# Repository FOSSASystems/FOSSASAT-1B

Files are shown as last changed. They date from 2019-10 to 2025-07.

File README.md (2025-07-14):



[Doxygen Documentation](https://fossasystems.github.io/FOSSASAT-1B)

## FOSSASAT-1B

FOSSASAT-1B is slightly modified second iteration of the FOSSASAT-1 satellite launched in December of 2019. It is set to launch with FOSSASAT-2 aboard the Alpha Firefly rocket in Q2-3 2020 into a 300km LEO orbit. The following differences are listed:

- Use of IXYS Cells instead of TrisolX
- No deployable Solar Panels
- Use of a new through-hole burnwire resistor
- Diodes added in MPPT
- DRF1268 has RST and SW connections modified
- Added Watchdog external connection for programming
- Passive attitude control re-designed

<br>
Picture of FOSSASAT-1B (Left) next to FOSSASAT-2
<br>
<br>


<br>

## Launch

FOSSASAT-1B was initially launched in the maiden mission of the firefly Alpha which experienced in an in-flight failure, subsequently it was launched into space on a second Firefly Alpha vehicle in October of 2022. Below is the first packet received from space! The satellite re-entered after 2 days in orbit due to a low insertion altitude. 

<br>

<br>

## Hardware

PCBs and Schematics are designed using EasyEDA, Java files are available for using them in said interface. 

## Software

The design of the FOSSASAT-1 code is a minimalist C-type structure. Everything is contained within code files whos name represents the functionality of the funtions within.

The core of the communications system uses a large switch that routes received messages to function calls.

The system has a large amount of configuration defines that control all aspects, this is found in the configuration.h/.cpp which again is documented thoroughly to describe it. There is a single function within the configuration "module" that controls the pin setups that can be found here: https://github.com/FOSSASystems/FOSSASAT-1B/blob/master/software/FossaSat1B/configuration.cpp#L32

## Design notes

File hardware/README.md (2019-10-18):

# FOSSASAT-1B Hardware
This folder contains all schematic, layout and mechanical files related to FOSSASAT-1B.

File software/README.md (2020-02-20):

# FOSSASAT-1B Software
This folder contains all software related to FOSSASAT-1B, on-board or otherwise.

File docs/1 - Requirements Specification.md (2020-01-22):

# 1 - Requirements

## Changelog

|Date|Description|Author|
|--|--|--|
|08/01/2020|Created initial document.|RB|
|08/01/2020|Added HREQ1 to HREQ25.|RB|
|08/01/2020|Added LREQ1 to LREQ5.|RB|
|08/01/2020|Merged FOSSASAT-1 requirements.|RB|
|09/01/2020|Modified requirement for transmissions modes to CW and FSK|RB|

## High Level Requirements Specification
|ID|Description|Author|Functional Requirements (Y/N)|Reference IDs|
|--|--|--|--|--|
|HREQ1|The satellite shall communicate with other generic and widely used radio systems.|RB|Y||
|HREQ2|The satellite must be able to be silenced with a radio command.|RB|Y||
|HREQ3|The satellite must transmit with a callsign.|RB|Y||
|HREQ4|The satellite must protect sensitive commands with encryption|RB|Y||
|HREQ5|The satellite must be able to operate from a battery.|RB|Y||
|HREQ6|The satellite must be able to re-charge the battery using solar panels.|RB|Y||
|HREQ7|The satellite must deploy its antenna|RB|Y||
|HREQ8|The satellite must be able to give a ground station its system information on command.|RB|Y||
|HREQ9|The radio power and operation shall not exceed or violate the regulated standards.|RB|Y||
|HREQ10|The radio communications shall not harm other radio communicating devices.|RB|Y||
|HREQ11|The satellite must be able to restart on command.|RB|Y||
|HREQ12|The satellite must be able to operate with no MCU issues such as memory leaking or halting.|RB|Y||
|HREQ13|The satellite must power on once it is jettisonned|RB|Y||
|HREQ14|The satellite must be able to orbit for at least 1 year.|RB|Y||
|HREQ15|The satellite's radio must be able to be configured remotely.|RB|Y||
|HREQ16|The satellite must be able to handle software and hardware errors.|RB|Y||
|HREQ17|The communications protocol shall be open source.|RB|N||
|HREQ18|The communications protocol must be accessible and simple.|RB|N||
|HREQ19|There must be no malicious transmisions.|RB|N||
|HREQ20|The satellite must be able to operate in a low power mode.|RB|Y||
|HREQ21|The satellite's hardware must be able to withstand all operational conditions.|RB|Y||
|HREQ22|The satellites hardware must be destroy in the atmosphere when de-oribiting.|RB|Y||
|HREQ23|The satellite's oribtal TLE must be available to the public.|RB|Y||
|HREQ24|The satellite must be registered with Satnogs to ensure ground station coverage.|RB|N||
|HREQ25|The satellite must not affect other satellites during launch.|RB|Y||
|HREQ26|The satellite must be able to communicate using the FOSSA Protocol.|RB|Y||

## Low Level Requirements
|Requirement ID|Description|Functional (Y/N)|Author|Reference IDs|
|--|--|--|--|--|
|LREQ1|The satellite must be able to trasmit using CW|Y|RB||
|LREQ2|The satellite must be able to trasmit using GFSK|Y|RB||
|LREQ3|The battery must stop charging if the temperature goes below 0 degrees Celsius.|Y|RB||
|LREQ4|The satellite must enter a low power mode when not in use.|Y|RB||
|LREQ5|Low power mode must be saved and retrieved from EEPROM|Y|RB||
|LREQ6|The callsign must be saved and retrieved from EEPROM|Y|RB||
|LREQ7|The battery temperature switching state must be saced and retrieved from EEPROM.|Y|RB||
|LREQ8|The radio's frequency band must be able to switch between X.XXX, Y.YYY,Z.ZZZ.etc|Y|RB||
|LREQ9|The radio's spreading factor must be able to switch between X,Y,Z.etc|Y|RB||
|LREQ10|The radio's sync word must be compatible with all devices.|Y|RB||
|LREQ11|The satellite must be able to communicate using Morse Code.|Y|RB||
|LREQ12|The satellite must stop transmissions when X command received..|Y|RB||

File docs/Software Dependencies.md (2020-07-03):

# FOSSASAT-1B Software Dependencies
The following is a list of all libraries and other dependencies required to build software for FOSSASAT-1B.

## Platform & Core Libraries
* AVR core

## Libraries
* FOSSA-Comms: https://github.com/FOSSASystems/FOSSA-Comms
* RadioLib: https://github.com/jgromes/RadioLib
* tiny-AES-c: https://github.com/FOSSASystems/tiny-AES-c
* INA226: https://github.com/jarzebski/Arduino-INA226
* AVR Low Power: https://github.com/canique/Low-Power-Canique

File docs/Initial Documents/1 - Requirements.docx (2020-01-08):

# 1 – Requirements

FOSSASAT-1B

FOSSA Systems

# Changelog

Date | Description | Author
08/01/2020 | - Created initial document. - Added HREQ1 to HREQ25 - Added LREQ1 to LREQ5 - Merged initial requirements and separated into high and low level. | Richard Bamford

# High Level Requirements Specification

ID | Description | Author | Functional requirement? (Y/N) | Reference ID
HREQ1 | The satellite shall communicate with other generic and widely used radio systems. | Richard Bamford | Y
HREQ2 | The satellite must be able to be silenced via a command. | Richard Bamford | Y
HREQ3 | The satellite must transmit with a callsign for identification. | Richard Bamford | Y
HREQ4 | The satellite must protect sensitive commands with AES encryption. | Richard Bamford | Y
HREQ5 | The satellite must be able to operate from a battery. | Richard Bamford | Y
HREQ6 | The satellite must be able to re-charge using the solar panels. | Richard Bamford | Y
HREQ7 | The satellite must deploy its solar panels. | Richard Bamford | Y
HREQ8 | The satellite must be able to give a ground station its system information on command. | Richard Bamford | Y
HREQ9 | The radio power and operation shall not exceed or violate the regulated standards. | Richard Bamford | Y
HREQ10 | The radio communications shall not harm other radio communicating devices. | Richard Bamford | Y
HREQ11 | The satellite must be able to restart itself on command. | Richard Bamford | Y
HREQ12 | The satellite must be able to operate with no MCU issues such as memory leaking/halting. | Richard Bamford | Y
HREQ13 | The satellite must switch on once it is jettisoned. | Richard Bamford | Y
HREQ14 | The satellite must be able to orbit for at least 1 year. | Richard Bamford | Y
HREQ15 | The satellite’s radio must be able to be configured remotely. | Richard Bamford | Y
HREQ16 | The satellite must be able to handle software and hardware errors. | Richard Bamford | Y
HREQ17 | The communications protocol shall be open source. | Richard Bamford | N
HREQ18 | The communications protocol must be accessible and therefore simple. | Richard Bamford | N
HREQ19 | There shall be no malicious transmissions. | Richard Bamford | N
HREQ20 | The satellite must be able to operate at a low power mode. | Richard Bamford | Y
HREQ21 | The satellite’s hardware must be able to withstand operational conditions. | Richard Bamford | Y
HREQ22 | The satellite’s hardware must be destroyed on de-orbiting. | Richard Bamford | Y
HREQ23 | The satellite’s orbital TLE must be available to the public. | Richard Bamford | N
HREQ24 | The satellite must be registered with Satnogs to ensure ground station coverage. | Richard Bamford | Y
HREQ25 | The satellite must remain in a benign state during launch. | Richard Bamford | Y
HREQ26 | The satellite must be able to communicate using the FOSSA Protocol. | Richard Bamford | Y

# Low Level Requirements Specification

Requirement ID | Description | Author | Reference IDs
LREQ1 | The satellite must be able to transmit using RTTY. | Richard Bamford | HREQ1
LREQ2 | The satellite must be able to transmit using LoRa. | Richard Bamford | HREQ1
LREQ3 | The battery must stop charging if temperature goes below 0 degrees Celsius. | Richard Bamford | HREQ5
LREQ4 | The satellite must enter a low power mode when not in use. | Richard Bamford | HREQ14
LREQ5 | Low power mode must be saved and retrieved from EEPROM. | Richard Bamford
LREQ6 | Callsign must be saved and retrieved from EEPROM. | Richard Bamford
LREQ7 | The battery temperature switch must be saved and retrieved from EEPROM. | Richard Bamford
LREQ8 | The frequency band must be able to switch between X.XXX, Y.YYY, Z.ZZZ | Richard Bamford | HREQ1, HREQ9
LREQ9 | The spreading factor must be able to switch between X,Y,Z | Richard Bamford | HREQ9
LREQ10 | The sync word must be compatable with all devices, set to X | Richard Bamford
LREQ11 | The satellite must be able to communicate using Morse Code. | Richard Bamford | HREQ1
LREQ12 | The satellite must stop transmissions when X command received.

# Bibliography

There are no sources in the current document.

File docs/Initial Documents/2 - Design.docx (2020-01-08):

# 2 – Design

FOSSASAT-1B

FOSSA Systems

# Changelog

Date | Description | Author
08/01/2020 | - Created initial document. | Richard Bamford

# Protocol Design

# Software Design

# Hardware Design

# Bibliography

There are no sources in the current document.

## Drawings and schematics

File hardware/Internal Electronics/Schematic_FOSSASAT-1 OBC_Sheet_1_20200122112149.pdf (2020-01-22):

## DEPLOYMENT FET

UTILITY HEADER | PROGRAMMING HEADER

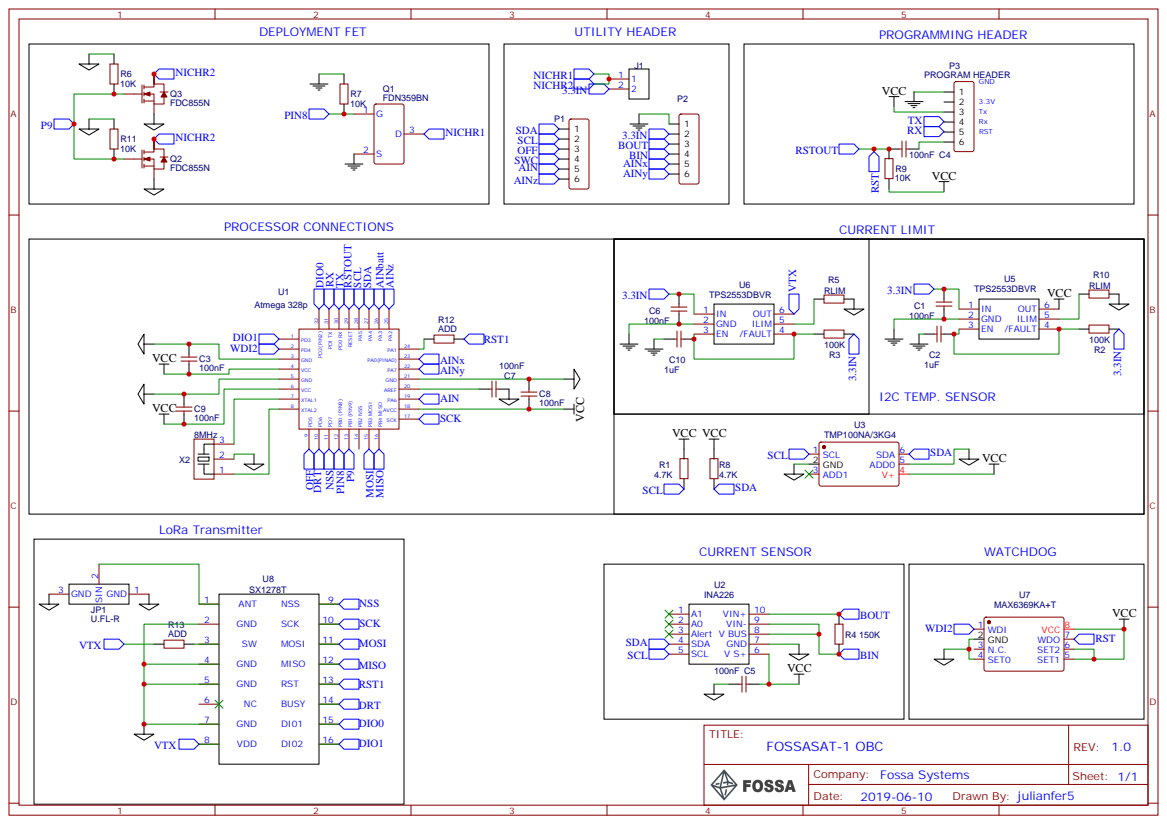
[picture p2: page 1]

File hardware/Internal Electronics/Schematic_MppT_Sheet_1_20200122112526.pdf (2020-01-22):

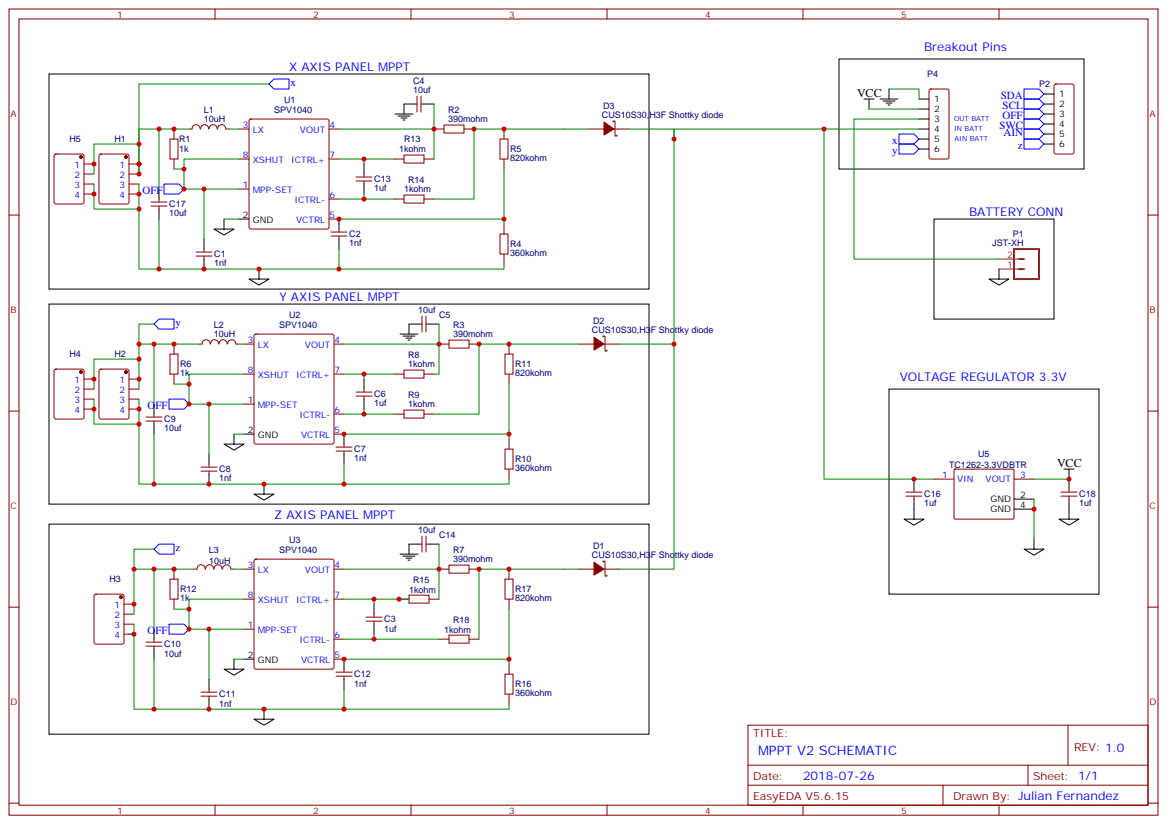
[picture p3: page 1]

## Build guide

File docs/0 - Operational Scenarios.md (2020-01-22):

# 0 - Operational Scenarios

## Changelog

|Date|Description|Author|
|--|--|--|
|08/01/2020|Created initial document.|RB|
|20/01/2020|Added initial Scenarios.|Julian Fernandez|

## On The Ground

See document 3. for testing to be carried out on the satellite before integration procedure.

|Name|Description|
|--|--|
|Integration Test|Satellite must be programmed, tested and charged beforehand, if neccesary due to time; check battery voltage via EGSE and serial output, antenna must not deploy in duration of test (3 minutes)|
|Integration Procedure|Satellite timer for deployer is reset via killswitches and then inserted into deployer. EEPROM counter still 0 as no deployment has occured|

## During Launch
|Name|Description|
|--|--|
|Storage Period|Satellite will stay in storage for several weeks without power with killswitches active|
|Launch|Satellite must withstand launch forces, no effect on Software|
## Jettison and Deployment
|Name|Description|
|--|--|
|Initial Jettison|Satellite is activated, Reset counter at 0 hence deployment procedure started|
|Deployment|If battery above x voltage When 3 minutes passed, burn wire for y seconds, else, wait for battery to reach y voltage.
|Wait time|During wait time, satellite is active but not transmitting (like in low power mode), it can recieve.
|Deployment Try 2|If time elapsed is more than 5 hours (timer integrated or cycle counter?), deploy in any case.
|Actual Deployment|When deployment command is carried out, start transmitting.

## Anomalies 
|Name|Description|
|--|--|
|In orbit resets|If satellite resets (can be issued by command or caused by watchdog), counter is increased. For the first 2 resets, deployment procedure occurs in the same manner as explained above|
|Deployment Command|Deployment Command bypasses voltage check|

## Orbital

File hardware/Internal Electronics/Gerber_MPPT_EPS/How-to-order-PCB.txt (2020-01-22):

How to Order PCB

Please refer to:
https://docs.easyeda.com/en/PCB/Order-PCB

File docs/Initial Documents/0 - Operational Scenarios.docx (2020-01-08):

# 0 – Operational Scenarios

FOSSASAT-1B

FOSSA Systems

# Changelog

Date | Description | Author
08/01/2020 | - Created initial document. | Richard Bamford

# On ground operation

# During launch operation

# Jettison operation

# Orbital operation

# Bibliography

There are no sources in the current document.

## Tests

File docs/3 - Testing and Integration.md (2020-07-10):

# 3 - Testing and Integration

## Changelog
|Date|Description|Author|
|--|--|--|
|08/01/2020|Created initial document.|RB|
|27/01/2020|Updated to include successful test result.|RB|
|5/07/2020|Entire test cases implemented in the software test system.|RB|
|06/07/2020|Added new document 3.1 Testing Additions|RB|

## Testing

Use your discretion when intrepreting the successful result of a test, if unsure, contact FOSSA Systems at our discord channel.

## Required Features for tests:

1. Controlling the temperature readings.
2. Controlling battery readings.
3. Checking whether deployment system has physically ran.
4. Detecting radio transmissions and interpreting them.
5. Manually making the satellite restart without losing test run.

### Main Program
|Reference ID|Description|Tested (Y/N)|Tested Date (dd-mm-yyyy|Status|Successful Result|Automated|
|--|--|--|--|--|--|--|
|MAINPROGT1|Startup configuration.||||Once the program has started, are all the pins, components and internal code configured correctly? Do they match the indended use?||
|MAINPROGT2|Test pin configuration.||||Do all pins attach to their intended component pin correctly?||
|MAINPROGT3|Test radio error mode handling.|||| Are all the radio exceptions created handled?| |
|MAINPROGT4|Confirm the MCU has enough resources to run the software.||||When the software is executed on the target hardware, does it run the entire program without having memory issues?.||
|MAINPROGT5|Check that the satellite transmits.|||| Can the satellite transmissions be received by a radio?
|MAINPROGT6|Check that the satellite can recieve trasmissions.|||| Can the satellite receive transmissions?|
|MAINPROGT7|Check that the radio re-configures successfully.||||When the radio is changed, does the satellite still transmit and receive correctly?|
|MAINPROGT8|Check that the MCU can be delayed by up to 10 minutes.||||When the satellite is delayed, does it react the way you intended?|
|MAINPROGT9|Check that the MCU can run the software system for at least a week.||||When you run the software on the related hardware, does it run how it should for a long time?| 
|MAINPROGT10|Check that the hardware watchdog is signalled correctly.||||Does the hardware watchdog cause any issues with restarting during its operation? For example causing restarts in long functions?|
|MAINPROGT11|Check that the hardware watchdog does not switch the satellite off during transmission.||||When the satellite transmits in any mode, does it correctly send transmissions without the watchdog interefering, even with long transmissions|
|MAINPROGT12|Check the software does not enter any restart loops.||||Does the code of the satellite enter any sections of code that cause it to restart over and over again? (check restart command useage)|

## Deployment
|Reference ID|Description|Tested (Y/N)|Tested Date (dd-mm-yyyy|Status|Successful Result|Automated|
|--|--|--|--|--|--|--|
|DEPLOYT1|Test the deployment sequence in scenarios; debugging, integration and jettison.||||Does the deployment sequence run correctly in these 3 scenarios? the debugging deployment sequence, integration and jettison sequences are different.|N - cannot simulate scenarios|
|DEPLOYT2|Check that the deployment sequence writes to the EEPROM.|||| When the deployment sequence runs in jettison mode, does it correctly save its state to the EEPROM?| Y |
|DEPLOYT3|Check that the deployment sequence does not run if the EEPROM state has been set.||||If the deployment sequence has ran, does it run again?|N - cannot test whether deployment has happened other than the EEPROM state.|
|DEPLOYT4|Check that the deployment sequence enable time is suitable.||||When the satellite powers the deployment mechanism, does it work correctly?|N - no way to measure whether the deployment sequence actually physically worked.|
|DEPLOYT5|Confirm that a system information transmission is sent before the deployment sequence begins.||||Before the deployment sequence begins, does it send a transmission to notify receivers that it is about to occur?|N - cannot test TX messages yet.|
|DEPLOYT6|Check that the deployment sequence transmits a success transmission afterwards.||||After the deployment sequence, does it tell receivers that it has occured?|N - cannot test radio TX.|
|DEPLOYT7|Check that the deployment system returns the correct value for its current state.||||When the satellite restarts, does it load the correct value from the EEPROM?|N - cannot simulate scenarios.|

## Power Control
|Reference ID|Description|Tested (Y/N)|Tested Date (dd-mm-yyyy|Status|Successfull Result|Automated|
|--|--|--|--|--|--|--|
|POWCONT1|Check the battery charging state changes when the temperature is >0 and <0 degrees Celsius.||||Simulate the sub-0 scenario by override the temperature sensor, does the battery charging react accordingly?|N - Cannot test this since we cannot simulate temperatures.|
|POWCONT12|Check the battery charging circuit (MPPT) is switched on and off correctly.||||When using the MPPT circuit, does it switch on and off without affecting other areas of code? (check call graph)||

## Automatic Interval Control
|Reference ID|Description|Tested (Y/N)|Tested Date (dd-mm-yyyy|Status|Successful Result|Automated|
|--|--|--|--|--|--|--|
|AUTOINT1|Check that the intervals returned for a given battery charged level matches the specified table of delays.||||Simulate the battery charging level at the specified thresholds (using bounds testing too) and check the interval changes according to the specified delays (see Julian for spec)|N - Cannot test this since we cannot simulate temperatures.|
|AUTOINT2|Check that the maximum and minimum intervals do not cause errors. (resetting loops)||||When the satellite is delayed, does it restart when it should? does it get into a restart loop anywhere? check this|Y|
|AUTOINT3|Check if the low power mode is enabled, if so force delay.||||If the low power mode is enabled, then make sure that the maximum interval for battery charging is used to maximise charging.|Y|
|AUTOINT4|Check if the interval control is disabled, if so force no delay.||||If the interval control is disabled, then test that there is no interval delay.|N - cannot automate this since interval enable/disable is hardcoded using macro define.|

## Hardware Interface
|Reference ID|Description|Tested (Y/N)|Tested Date (dd-mm-yyyy|Status|Successful Result|
|--|--|--|--|--|--|
|HARDINT1|Test the bounds and normal readings of voltages. (Volts)||||Check that the voltage readings are ok, different scenarios such as broken component, disconnected component.etc|
|HARDINT2|Check that the battery voltage is output when the MPPT is disabled.||||When the MPPT is disabled, make sure that the battery voltage is output.|
|HARDINT3|Check that the battery charging voltage is output when the MPPT is enabled. (Volts)||||When the MPPT is enabled, double check that the voltage it reads matches the battery charging voltage.|
|HARDINT4|Test that the satellite restarts when the hardware watchdog is not given a signal.||||Disconnect the watchdog, does the satellite restart?|
|HARDINT5|Check that the battery charging voltage is output correctly. (Amperes)||||Doublecheck that the battery charging voltage reads correct values i.e. values that make sense.|
|HARDINT6|Check that the battery voltage reading is output correctly. (Volts)||||double check that the battery voltage read is correct and makes sense.|
|HARDINT7|Check that the solar cell's voltage readings are correct. (Volts)||||Double check the voltage readings.|
|HARDINT8|Check that the battery temperature reading is correct. (Celsius)||||Double check the battery temperature readings are ok.|
|HARDINT9|Check that the battery voltage reading is output correctly.||||Double check that the battery voltage|
|HARDINT10 (REMOVED DUPLICATE OF HARDINT7)|Check that the watchdog heartbeat signal can be enabled and disabled. (REMOVED DUPLICATE OF HARDINT7)|(REMOVED DUPLICATE OF HARDINT7)|(REMOVED DUPLICATE OF HARDINT7)|(REMOVED DUPLICATE OF HARDINT7)|(REMOVED DUPLICATE OF HARDINT7)|
|HARDINT11|Check that the sensors are configured correctly.||||Look at all the sensor readings together, do they all make sense?|

## Safety & Security
|Reference ID|Description|Tested (Y/N)|Tested Date (dd-mm-yyyy|Status|Successful Result|
|--|--|--|--|--|--|
|SAFESECT1|Check that the satellite correctly handles LoRa radio codes.||||When the radio outputs errors, how are they handled? check the failure modes - consult team discord to report unknown failure mode reponses.|
|SAFESECT2|Check that the transmissions content are safe and secure.||||Transmissions do not affect other satellites negatively, make sure encrypted transmissions are encrypted by receiving them.|
|SAFESECT3|Check that the EEPROM values for errors and handle them.||||If the eeprom values return errors, how are they handled?|

## Communication
|Reference ID|Description|Tested (Y/N)|Tested Date (dd-mm-yyyy|Status|Successful Result|
|--|--|--|--|--|--|
|COMMST1|Test the enable and disabling of transmissions.||||When the transmissions are enabled and disabled, does the satellite stop transmitting and start transmitting again correctly?|
|COMMST2|Test the repeater command.||||Send the satellite a repeater command and receive it with a radio.|
|COMMST3|Test the ping-pong command.||||Send a PING command to the satellite and receive a PONG command from a seperate radio.|
|COMMST4|Test the callsign change command.||||Send the satellite a callsign change command and then receive a transmissions of the new callsign|
|COMMST5|Test the command security features.||||Make sure protected security features cannot be invoked without permission|
|COMMST6|Test that the satellite transmits a notification when it powers on.|||||Check that when you start the satellite, it sends you information to validate that it has turned on|
|COMMST7|Test that the satellite transmits a notification after it deploys.||||Run a deployment sequence in jettison mode and then see if you can receive a transmission.|
|COMMST8|Test that the EEPROM is reset on command.||||
|COMMST9|Test the restart command.||||
|COMMST10|Test the frequency band changing command.||||
|COMMST11|Test the manual deployment command.||||
|COMMST12|Test the manual system information command.||||
|COMMST13|Test the satellite transmits when it shuts down.||||
|COMMST14|Check the transmission timing is correct.||||
|COMMST15|Check the callisgn is transmitted.||||
|COMMST16|Check the spreading factor changes do not break transmissions.||||
|COMMST17|Check the low power mode disable and enable command.||||
|COMMST18|Check the MPPT keep-alive command.||||
|COMMST19|Check the MPPT enable and disable command.||||

## System Verification and Validation

### Requirements Fulfilment

## Operation and Maintenance

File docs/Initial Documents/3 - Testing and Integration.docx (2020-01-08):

# 3 – Testing and Integration

FOSSASAT-1B

FOSSA Systems

# Changelog

Date | Description | Author
08/01/2020 | - Created initial document. | Richard Bamford

# Testing

## Test Schedule

### Hardware

### Software

# System Verification and Validation

## Requirements Fulfilment

# Operation and Maintenance

# Bibliography

There are no sources in the current document.

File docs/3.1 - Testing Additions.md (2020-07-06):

# 3.2 - Testing and Integration (Additions)

## Changelog

| Date | Description | Author |
| --- | --- | --- |
| 06/07/2020 | Created initial document. | RB |

## Deployment

| Reference ID | Description | Tested (Y/N) | Tested Date (dd-mm-yyyy | Status | Successful Result | Automated |
| --- | --- | --- | --- | --- | --- | --- |
| DEPLOYT8 | Test that the deployment system can run over the size of uint8_t used to track its number. | | | | Successful result is that the number  cleanly loops to 0. | Y |

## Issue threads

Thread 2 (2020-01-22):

Deployment sensing

rmely, 2020-01-22:
I am not sure how the deployment circuit works, as the schema is not available, but I believe it is a MOSFET driver to burn the wire.
My suggestion would be to add a resistor with low value and good dissipation between the MOSFET output and the wire, creating a potential difference between the battery voltage, where it would be possible to measure the current passing through the driver using an MCU ADC.

First, with this value it would be possible to know when the wire is broken, thus enabling the PA that would have been disabled until then.
Mechanical or optical sensors on the panels would also be interesting.
Also send this information to the GS.

Second, with this value it would be possible to define the duty cycle of a PWM that would control the MOSFET, creating an overcurrent protection circuit and a constant current on the wire.
So replacing the code and functionality of the Deployment_Deploy () function;
This code should be driven by an interruption.

As a backup measure, the values   for decision making should be saved in the EEPROM and be subject to change via GS.

Thank you for your attention and work on this project.
Rodrigo Ely

jgromes, 2020-01-22:
@juliantech5 thoughts on this?

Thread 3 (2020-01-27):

Deployment MOSFETs could be enabled 1 at a time.

mcsarge, 2020-01-27:
I think it might be a good idea to actuate each MOSFET 1 at a time. This would allow the full current of the battery to burn one wire at a time, allowing more current to each to be sure they burn. This would also allow the deployment to work in a nominal voltage situation.

mcsarge, 2020-01-27:
// burn the nichrome wire
  digitalWrite(DIGITAL_OUT_MOSFET_1, HIGH);

  // wait for 0.5 second
  Power_Control_Delay(600, false);

  // set MOSFET low
  digitalWrite(DIGITAL_OUT_MOSFET_1, LOW);

  // burn the nichrome wire
  digitalWrite(DIGITAL_OUT_MOSFET_2, HIGH);

  // wait for 0.5 second
  Power_Control_Delay(600, false);

  // set MOSFET low
  digitalWrite(DIGITAL_OUT_MOSFET_2, LOW);

jgromes, 2020-01-28:
Seems like a reasonable idea, @juliantech5 your thoughts on this (in regards to the new deployment system)?

juliantech5, 2020-01-28:
The output of the MOSFETS on FOSSASAT-1B are parallel, the idea behind
using two different MOSFETs it simply to have a redundant system and to
spread the load across to devices instead of one. This idea, however,
should be used on FOSSASAT-2 which has separate burn resistors, thanks for
the suggestion.

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

--

*Julian Fernandez*

*Fossa Systems*

*CEO & Co-Founder*

*_____________________________*
Website: *fossa.systems <http://fossa.systems/>*

mcsarge, 2020-01-29:
Oh, OK I understand - I should have looked at the schematic :-(

jgromes, 2020-02-07:
Implemented in [FOSSASAT-2](https://github.com/FOSSASystems/FOSSASAT-2)

Closed 2020-02-07.

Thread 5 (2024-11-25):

SolarPanelAntenna PCB

hanno23, 2024-11-25:
The Solar Panels on the PCB with the UHF antenna are all short circuited to GND when I import the JSON File to EasyEDA.

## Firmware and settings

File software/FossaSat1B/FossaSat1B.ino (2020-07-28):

/**
 * @file FossaSat1B.ino
 * @author FOSSA Systems
 * @brief
 *
 */

#include "FossaSat1B.h"

// compile-time checks
#if (!defined(RADIOLIB_VERSION)) || (RADIOLIB_VERSION < 0x04000000)
  #error "Unsupported RadioLib version (< 4.0.0)!"
#endif

#if !defined(RADIOLIB_STATIC_ONLY)
  #error "RadioLib is using dynamic memory management, make sure static only is enabled in RadioLib/src/BuildOpt.h"
#endif

#ifndef UNIT_TEST
// cppcheck-suppress unusedFunction
void setup() {
  // initialize debug port
  FOSSASAT_DEBUG_PORT.begin(FOSSASAT_DEBUG_SPEED);
  FOSSASAT_DEBUG_PORT.println();

  // increment reset counter
  FOSSASAT_DEBUG_PORT.print('R');
  FOSSASAT_DEBUG_PORT.println(Persistent_Storage_Read<uint16_t>(EEPROM_RESTART_COUNTER_ADDR));
  Persistent_Storage_Increment_Counter(EEPROM_RESTART_COUNTER_ADDR);

  // setup pins
  Configuration_Setup_Pins();

  // check if this is the first run
  if(Persistent_Storage_Read<uint8_t>(EEPROM_FIRST_RUN_ADDR) != EEPROM_CONSECUTIVE_RUN) {
    // first run, set EEPROM flag
    Persistent_Storage_Write<uint8_t>(EEPROM_FIRST_RUN_ADDR, EEPROM_CONSECUTIVE_RUN);

  } else {
    // consecutive run, load power control configuration
    Power_Control_Load_Configuration();

  }

  // print power configuration
  FOSSASAT_DEBUG_PORT.print('C');
  FOSSASAT_DEBUG_PORT.println(powerConfig.val, BIN);

  // set temperature sensor resolution
  Pin_Interface_Set_Temp_Resolution(BOARD_TEMP_SENSOR_ADDR, TEMP_SENSOR_RESOLUTION_10_BITS);
  Pin_Interface_Set_Temp_Resolution(BATTERY_TEMP_SENSOR_ADDR, TEMP_SENSOR_RESOLUTION_10_BITS);

  // setup INA226
  #ifdef ENABLE_INA226
    Power_Control_Setup_INA226();
  #endif

  // setup radio
  FOSSASAT_DEBUG_PORT.print('L');
  FOSSASAT_DEBUG_PORT.println(Communication_Set_Modem(MODEM_LORA));
  FOSSASAT_DEBUG_PORT.print('F');
  FOSSASAT_DEBUG_PORT.println(Communication_Set_Modem(MODEM_FSK));

  #ifdef ENABLE_INA226
    FOSSASAT_DEBUG_PORT.print('I');
    FOSSASAT_DEBUG_PORT.println(Power_Control_INA226_Check());
  #endif

  // check deployment
  #ifdef ENABLE_DEPLOYMENT_SEQUENCE
    uint8_t attemptNumber = Persistent_Storage_Read<uint8_t>(EEPROM_DEPLOYMENT_COUNTER_ADDR);

    FOSSASAT_DEBUG_PORT.print('D');
    FOSSASAT_DEBUG_PORT.println(attemptNumber);
    delay(10);

    // check number of deployment attempts
    if (attemptNumber == 0) {
      // integration, reset system info
      Persistent_Storage_Wipe();

      // print sensor data for integration purposes (independently of FOSSASAT_DEBUG macro!)
      uint32_t start = millis();
      uint32_t lastSample = 0;
      while (millis() - start <= (uint32_t)DEPLOYMENT_DEBUG_LENGTH * (uint32_t)1000) {
        // check if its time for next measurement
        if (millis() - lastSample >= (uint32_t)DEPLOYMENT_DEBUG_SAMPLE_PERIOD) {
          lastSample = millis();
          FOSSASAT_DEBUG_PORT.println();

          #ifdef ENABLE_INA226
            FOSSASAT_DEBUG_PORT.print(F("Chr V\t"));
            FOSSASAT_DEBUG_PORT.println(Power_Control_Get_Charging_Voltage(), 2);

            FOSSASAT_DEBUG_PORT.print(F("Chr mA\t"));
            FOSSASAT_DEBUG_PORT.println(Power_Control_Get_Charging_Current(), 3);

            FOSSASAT_DEBUG_PORT.print(F("Bat V\t"));
            FOSSASAT_DEBUG_PORT.println(Power_Control_Get_Battery_Voltage(), 2);
          #endif

          FOSSASAT_DEBUG_PORT.print(F("SolA V\t"));
          FOSSASAT_DEBUG_PORT.println(Pin_Interface_Read_Voltage(ANALOG_IN_SOLAR_A_VOLTAGE_PIN), 2);

          FOSSASAT_DEBUG_PORT.print(F("SolB V\t"));
          FOSSASAT_DEBUG_PORT.println(Pin_Interface_Read_Voltage(ANALOG_IN_SOLAR_B_VOLTAGE_PIN), 2);

          FOSSASAT_DEBUG_PORT.print(F("SolC V\t"));
          FOSSASAT_DEBUG_PORT.println(Pin_Interface_Read_Voltage(ANALOG_IN_SOLAR_C_VOLTAGE_PIN), 2);

          FOSSASAT_DEBUG_PORT.print(F("Bat C\t"));
          FOSSASAT_DEBUG_PORT.println(Pin_Interface_Read_Temperature(BATTERY_TEMP_SENSOR_ADDR), 2);

          FOSSASAT_DEBUG_PORT.print(F("Brd C\t"));
          FOSSASAT_DEBUG_PORT.println(Pin_Interface_Read_Temperature(BOARD_TEMP_SENSOR_ADDR), 2);

          FOSSASAT_DEBUG_PORT.print(F("MCU C\t"));
          FOSSASAT_DEBUG_PORT.println(Pin_Interface_Read_Temperature_Internal());

          FOSSASAT_DEBUG_PORT.print(F("RST\t\t"));
          FOSSASAT_DEBUG_PORT.println(Persistent_Storage_Read<uint16_t>(EEPROM_RESTART_COUNTER_ADDR));

          FOSSASAT_DEBUG_PORT.print('C');
          Power_Control_Load_Configuration();
          FOSSASAT_DEBUG_PORT.println(powerConfig.val, BIN);

          FOSSASAT_DEBUG_PORT.println();
        }

        // pet watchdog
        if (millis() - lastHeartbeat >= WATCHDOG_LOOP_HEARTBEAT_PERIOD) {
          lastHeartbeat = millis();
          Pin_Interface_Watchdog_Heartbeat();
        }
      }

      // increment deployment counter
      FOSSASAT_DEBUG_PORT.println(F("INTDONE"));
      Persistent_Storage_Write<uint8_t>(EEPROM_DEPLOYMENT_COUNTER_ADDR, attemptNumber + 1);
      Power_Control_Delay(DEPLOYMENT_SLEEP_LENGTH, true, true);

    } else if(Persistent_Storage_Read<uint8_t>(EEPROM_DEPLOYMENT_COUNTER_ADDR) <= DEPLOYMENT_ATTEMPTS) {
      // sleep before deployment
      FOSSASAT_DEBUG_PRINT('S');
      FOSSASAT_DEBUG_PRINTLN(DEPLOYMENT_SLEEP_LENGTH);
      FOSSASAT_DEBUG_DELAY(10);
      Power_Control_Delay(DEPLOYMENT_SLEEP_LENGTH, true, true);

      // deploy
      Deployment_Deploy();
    }

  #endif

  // reset uptime counter
  Persistent_Storage_Write<uint32_t>(EEPROM_UPTIME_COUNTER_ADDR, 0);
}

// cppcheck-suppress unusedFunction
void loop() {
  // variable to measure time when not in sleep mode
  uint32_t activeStart = millis();

  // get loop number
  uint8_t numLoops = Persistent_Storage_Read<uint8_t>(EEPROM_LOOP_COUNTER);

  // check battery voltage
  FOSSASAT_DEBUG_PRINT('B');
  #ifdef ENABLE_INA226
  float battVoltage = Power_Control_Get_Battery_Voltage();
  #else
  float battVoltage = 3.99;
  #endif
  FOSSASAT_DEBUG_PRINTLN(battVoltage, 2);
  Power_Control_Check_Battery_Limit();
  FOSSASAT_DEBUG_PRINT('C');
  FOSSASAT_DEBUG_PRINTLN(powerConfig.val, BIN);

  // try to switch MPPT on (may be overridden by temperature check)
  Power_Control_Charge(true);

  // CW beacon
  bool beaconSent = false;
  Communication_Set_Modem(MODEM_FSK);
  FOSSASAT_DEBUG_DELAY(10);
  #ifdef ENABLE_TRANSMISSION_CONTROL
  if(!powerConfig.bits.transmitEnabled) {
    FOSSASAT_DEBUG_PRINTLN(F("Tx off"));
  } else {
  #endif

  if((battVoltage >= BATTERY_CW_BEEP_VOLTAGE_LIMIT) && (numLoops % MORSE_BEACON_LOOP_FREQ == 0)) {
    // transmit full Morse beacon
    Communication_Send_Morse_Beacon(battVoltage);
    beaconSent = true;
  } else {
    // set delay between beeps according to battery voltage
    float delayLen = battVoltage - MORSE_BATTERY_MIN;
    if(battVoltage < MORSE_BATTERY_MIN + MORSE_BATTERY_STEP) {
      delayLen = MORSE_BATTERY_STEP;
    }

    // this isn't the loop to transmit full Morse beacon, or the battery is low, transmit CW beeps
    for(uint8_t i = 0; i < NUM_CW_BEEPS; i++) {
      Communication_CW_Beep(500 * SLEEP_LENGTH_CONSTANT);
      Power_Control_Delay(delayLen * 1000 * SLEEP_LENGTH_CONSTANT, true);
    }
  }

  #ifdef ENABLE_TRANSMISSION_CONTROL
  }
  #endif

  // wait for a bit
  FOSSASAT_DEBUG_DELAY(10);
  Power_Control_Delay(500, true, true);

  // send FSK system info
  Communication_Set_Modem(MODEM_FSK);
  Communication_Send_System_Info();

  // wait for a bit
  FOSSASAT_DEBUG_DELAY(10);
  Power_Control_Delay(500, true, true);

  // send LoRa system info if not in low power mode
  Communication_Set_Modem(MODEM_LORA);
  #ifdef ENABLE_INTERVAL_CONTROL
  if(!powerConfig.bits.lowPowerModeActive) {
    Communication_Send_System_Info();
  }
  #else
    Communication_Send_System_Info();
  #endif

  // wait for a bit
  FOSSASAT_DEBUG_DELAY(10);
  Power_Control_Delay(500, true, true);

  // LoRa receive
  uint8_t windowLenLoRa = Persistent_Storage_Read<uint8_t>(EEPROM_LORA_RECEIVE_LEN_ADDR);
  FOSSASAT_DEBUG_PRINT(F("LR"));
  if(powerConfig.bits.lowPowerModeActive) {
    // use only half of the interval in low power mode
    windowLenLoRa /= 2;
  }
  FOSSASAT_DEBUG_PRINTLN(windowLenLoRa);
  radio.setDio1Action(Communication_Receive_Interrupt);
  radio.startReceive();

  for(uint8_t i = 0; i < windowLenLoRa * SLEEP_LENGTH_CONSTANT; i++) {
    Power_Control_Delay(1000, true);
    if(dataReceived) {
      radio.standby();
      Communication_Process_Packet();
      radio.startReceive();
    }
  }

  // GFSK receive
  uint8_t windowLenFsk = Persistent_Storage_Read<uint8_t>(EEPROM_FSK_RECEIVE_LEN_ADDR);
  Communication_Set_Modem(MODEM_FSK);
  FOSSASAT_DEBUG_PRINT(F("FR"));
  if(powerConfig.bits.lowPowerModeActive) {
    // use only half of the interval in low power mode
    windowLenFsk /= 2;
  }
  FOSSASAT_DEBUG_PRINTLN(windowLenFsk);
  radio.setDio1Action(Communication_Receive_Interrupt);
  radio.startReceive();

  for(uint8_t i = 0; i < windowLenFsk * SLEEP_LENGTH_CONSTANT; i++) {
    Power_Control_Delay(1000, true);
    if(dataReceived) {
      radio.standby();
      Communication_Process_Packet();
      radio.startReceive();
    }
  }

  radio.clearDio1Action();

  // set everything to sleep
  uint32_t interval = Power_Control_Get_Sleep_Interval();
  FOSSASAT_DEBUG_PRINT('S');
  FOSSASAT_DEBUG_PRINTLN(interval);
  FOSSASAT_DEBUG_DELAY(10);
  Power_Control_Delay(interval * SLEEP_LENGTH_CONSTANT, true, true);

  // update loop counter
  numLoops++;
  Persistent_Storage_Write<uint8_t>(EEPROM_LOOP_COUNTER, numLoops);

  // check automated deployment attempts
  uint32_t uptimeCounter = Persistent_Storage_Read<uint32_t>(EEPROM_UPTIME_COUNTER_ADDR);
  uint8_t attempts = Persistent_Storage_Read<uint8_t>(EEPROM_DEPLOYMENT_COUNTER_ADDR);
  if((attempts <= DEPLOYMENT_ATTEMPTS) && (uptimeCounter >= AUTODEPLOY_DELAY)) {
    // deployment attemp limit not reached yet, attempt more deployments
    Deployment_Deploy();
  }

  // update uptime counter
  uint32_t activeElapsed = (millis() - activeStart + 500)/1000;
  FOSSASAT_DEBUG_PRINT('a');
  FOSSASAT_DEBUG_PRINTLN(activeElapsed);

  uint32_t elapsedTotal = 2 + windowLenLoRa + windowLenFsk + activeElapsed + interval;
  if(beaconSent) {
    // transmitting full Morse beacon takes about 9 seconds
    elapsedTotal += 9;
  } else {
    elapsedTotal += NUM_CW_BEEPS;
  }
  FOSSASAT_DEBUG_PRINT('t');
  FOSSASAT_DEBUG_PRINTLN(elapsedTotal);

  uptimeCounter += elapsedTotal;
  Persistent_Storage_Write<uint32_t>(EEPROM_UPTIME_COUNTER_ADDR,  uptimeCounter);
}
#endif // UNIT_TEST

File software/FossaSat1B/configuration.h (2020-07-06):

#ifndef CONFIGURATION_H_INCLUDED
#define CONFIGURATION_H_INCLUDED

#include "FossaSat1B.h"

/**
 * @mainpage
 *
 * # NOTICE
 * The tests given here are only guidelines, please also refer to the FOSSASAT-1 software test plans and documentation for a complete view.
 *
 * # Navigation
 * - See the modules section for help with the satellite's configuration.
 * - Each header file contains documentation.
 *
 */

/**
 * @defgroup configuration_page Configuration
 * @brief

 * @{
 */

/**
 * @defgroup defines_string_memory_limits String Limits
 * @{
 */
#define MAX_STRING_LENGTH                               32			/*!< String length limit (bytes). */
#define MAX_OPT_DATA_LENGTH                             128			/*!< Optional data length limit (bytes). */
#define MAX_RADIO_BUFFER_LENGTH                         (MAX_STRING_LENGTH + 2 + MAX_OPT_DATA_LENGTH)     /*!< Radio buffer length limit. */

/**
 * @}
 */

/**
 * @defgroup defines_debug_macros Debug Macros (only comment out for debug usage.)
 *
 * @test (ID CONF_DEBUG_MACROS_T0) (SEV 1) Uncomment ENABLE_TRANSMISSION_CONTROL, test no transmissions are produced.
 * @test (ID CONF_DEBUG_MACROS_T1) (SEV 1) Uncomment ENABLE_DEPLOYMENT_SEQUENCE, test no deployment sequence ran (this define is for debugging purposes).
 * @test (ID CONF_DEBUG_MACROS_T2) (SEV 1) Uncomment ENABLE_INTERVAL_CONTROL, test that the battery voltages have no affect on the sleep duration.
 * @test (ID CONF_DEBUG_MACROS_T3) (SEV 1) Uncomment ENABLE_INA226, test that the current readings are correct.
 *
 * @{
 */
#define ENABLE_TRANSMISSION_CONTROL                                 /*!< Comment out to disable transmission control (transmission disable and no transmissions in low power mode) */
#define ENABLE_DEPLOYMENT_SEQUENCE                                  /*!< Comment out to disable deployment sequence */
#define ENABLE_INTERVAL_CONTROL                                     /*!< Comment out to disable automatic sleep interval and transmission control */
#define ENABLE_INA226                                               /*!< Comment out to skip INA226 reading */
/**
 * @}
 */


/**
 * @defgroup defines_power_management_configuration Power Management Configuration
 *
 * @test (ID CONF_POWER_MANAGEMENT_T0) (SEV 1) Check that the satellite switches to low power mode when its voltage goes below BATTERY_VOLTAGE_LIMIT.
 * @test (ID CONF_POWER_MANAGEMENT_T1) (SEV 2) Check that the satellite sends a morse beacon transmission when it switches to Low Power Mode.
 * @test (ID CONF_POWER_MANAGEMENT_T2) (SEV 1) Check that the battery stops charging when the temperature goes below this threshold, and starts charging again when it is not.
 * @test (ID CONF_POWER_MANAGEMENT_T3) (SEV 1) Check that the watchdog is signalled every WATCHDOG_LOOP_HEARTBEAT_PERIOD.
 * @test (ID CONF_POWER_MANAGEMENT_T4) (SEV 1) Check that the satellite sleeping times using the SLEEP_LENGTH_CONSTANT is suitable to account for the LowPower libraries overhead.
 * @test (ID CONF_POWER_MANAGEMENT_T5) (SEV 1) Check that the satellite does not deploy after DEPLOYMENT_ATTEMPS has reached.
 * @test (ID CONF_POWER_MANAGEMENT_T6) (SEV 1) Check that the satellite waits for this amount of time before the deploy sequence starts, this is for jettison.
 * @test (ID CONF_POWER_MANAGEMENT_T7) (SEV 5) Check that each debug print waits DEPLOYMENT_DEBUG_SAMPLE_PERIOD amount of time between each print.
 *
 * @todo Julian -> Set appropriate BATTERY_VOLTAGE_LIMIT and BATTERY_CW_BEEP_VOLTAGE_LIMIT
 *
 * @{
 */
#define BATTERY_VOLTAGE_LIMIT                           3.8f        /*!< Battery voltage limit to enable low power mode (V). */
#define BATTERY_CW_BEEP_VOLTAGE_LIMIT                   3.8f        /*!< Battery voltage limit to switch into morse beep (V). */
#define BATTERY_TEMPERATURE_LIMIT                       -0.7f       /*!< Battery charging temperature limit (deg. C). */
#define WATCHDOG_LOOP_HEARTBEAT_PERIOD                  1000        /*!< Watchdog heartbeat period in loop() (ms). */
#define WATCHDOG_RESET_NUM_SLEEP_CYCLES                 4           /*!< Number of 8-second sleep cycles to reset watchdog */
#define SLEEP_LENGTH_CONSTANT                           0.9         /*!< Sleep times are multiplied by this constant to compensate for the LowPower libraries overhead. */
#define DEPLOYMENT_ATTEMPTS                             4           /*!< Number of deployment attempts. */
#define DEPLOYMENT_SLEEP_LENGTH                         1800000     /*!< Sleep for this period of time before deployment (ms) */
#define DEPLOYMENT_DEBUG_LENGTH                         60          /*!< How long to wait until the debugging print routine breaks (s). See: FossaSat1B.ino */
#define DEPLOYMENT_DEBUG_SAMPLE_PERIOD                  1000        /*!< How long to wait between each debug parameter print (ms). See: FossaSat1B.ino */
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

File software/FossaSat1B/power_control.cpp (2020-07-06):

#include "power_control.h"

powerConfigBits_t powerConfigBits = {
  .lowPowerModeActive = LOW_POWER_MODE_ACTIVE,
  .lowPowerModeEnabled = LOW_POWER_MODE_ENABLED,
  .mpptTempSwitchEnabled = MPPT_TEMP_SWITCH_ENABLED,
  .mpptKeepAliveEnabled = MPPT_KEEP_ALIVE_ENABLED,
  .transmitEnabled = TRANSMIT_ENABLED
};

powerConfig_t powerConfig = {
  .bits = powerConfigBits
};

void Power_Control_Load_Configuration() {
  powerConfig.val = Persistent_Storage_Read<uint8_t>(EEPROM_POWER_CONFIG_ADDR);
}

void Power_Control_Save_Configuration() {
  Persistent_Storage_Write<uint8_t>(EEPROM_POWER_CONFIG_ADDR, powerConfig.val);
}

void Power_Control_Charge(bool charge) {
  FOSSASAT_VERBOSE_PRINT(F("MPPT "));
  FOSSASAT_VERBOSE_PRINTLN(charge);

  Power_Control_Load_Configuration();
  if(powerConfig.bits.mpptKeepAliveEnabled) {
    // force MPPT to float regardless of anything else
    FOSSASAT_VERBOSE_PRINTLN('K');
    pinMode(DIGITAL_OUT_MPPT_PIN, INPUT);
  } else if((Pin_Interface_Read_Temperature(BATTERY_TEMP_SENSOR_ADDR) < BATTERY_TEMPERATURE_LIMIT) && powerConfig.bits.mpptTempSwitchEnabled) {
    // force MPPT low, only if temperature switch is enabled
    FOSSASAT_VERBOSE_PRINTLN('L');
    pinMode(DIGITAL_OUT_MPPT_PIN, OUTPUT);
    digitalWrite(DIGITAL_OUT_MPPT_PIN, LOW);
  } else if(charge){
    // set MPPT to float
    pinMode(DIGITAL_OUT_MPPT_PIN, INPUT);
  } else {
    // set MPPT to low
    pinMode(DIGITAL_OUT_MPPT_PIN, OUTPUT);
    digitalWrite(DIGITAL_OUT_MPPT_PIN, LOW);
  }
}

uint32_t Power_Control_Get_Sleep_Interval() {
  // sleep interval in ms (default for battery > 3.7 V)
  uint32_t interval = 0;

  #ifdef ENABLE_INTERVAL_CONTROL
    // get battery voltage
    float batt = Power_Control_Get_Battery_Voltage();

    if(batt > 4.05f) {
      interval = (uint32_t)20 * (uint32_t)1000;
    } else if(batt > 4.0f) {
      interval = (uint32_t)35 * (uint32_t)1000;
    } else if(batt > 3.9f) {
      interval = (uint32_t)100 * (uint32_t)1000;
    } else if(batt > 3.8f) {
      interval = (uint32_t)160 * (uint32_t)1000;
    } else if(batt > 3.7f) {
      interval = (uint32_t)180 * (uint32_t)1000;
    } else {
      interval = (uint32_t)240 * (uint32_t)1000;
    }
  #endif

  return(interval);
}

void Power_Control_Delay(uint32_t ms, bool sleep, bool sleepRadio) {
  if(ms == 0) {
    return;
  }

  // calculate number of required loops (rounded up)
  float numLoops = 0.5f;
  if(sleep) {
    numLoops += (float)ms / 500.0;
  } else {
    numLoops += (float)ms / 50.0;
  }

  // set radio to sleep
  if(sleepRadio) {
    radio.sleep();
  }

  // perform all loops
  for(uint32_t i = 0; i < (uint32_t)numLoops; i++) {
    Pin_Interface_Watchdog_Heartbeat();
    if(sleep) {
      LowPower.powerDown(SLEEP_500MS, ADC_OFF, BOD_OFF);
    } else {
      delay(50);
    }

  }

  // wake up radio
  if(sleepRadio) {
    radio.standby();
  }
}

void Power_Control_Setup_INA226() {
  ina.begin(INA_ADDR);
  ina.configure(INA226_AVERAGES_1, INA226_BUS_CONV_TIME_1100US, INA226_SHUNT_CONV_TIME_1100US, INA226_MODE_SHUNT_BUS_CONT);
  ina.calibrate(INA_RSHUNT, INA_MAX_CURRENT);
}

bool Power_Control_INA226_Check() {
  // attempt to read manufacturer ID register
  Wire.beginTransmission(INA_ADDR);
  Wire.write(INA_REG_MANUFACTURER_ID);
  Wire.endTransmission();
  delay(1);

  // try to read
  Wire.requestFrom((uint8_t)INA_ADDR, (uint8_t)2);
  if(Wire.available() != 2) {
    return(false);
  }

  // check value
  uint8_t vha = Wire.read();
  uint8_t vla = Wire.read();
  uint16_t value = vha << 8 | vla;

  if(value != INA_MANUFACTURER_ID) {
    return(false);
  }

  return(true);
}

float Power_Control_Get_Battery_Voltage() {
  // try to switch MPPT off (may be overridden by MPPT keep alive)
  Power_Control_Charge(false);

  // get voltage
  float val = -999;
  if(Power_Control_INA226_Check()) {
    val = ina.readBusVoltage();
  }

  // try to switch MPPT on (may be overridden by temperature check)
  Power_Control_Charge(true);

  return(val);
}

float Power_Control_Get_Charging_Voltage() {
  if(!Power_Control_INA226_Check()) {
    return(-999.0);
  }
  return(ina.readBusVoltage());
}

float Power_Control_Get_Charging_Current() {
  if(!Power_Control_INA226_Check()) {
    return(-999.0);
  }
  return(ina.readShuntCurrent());
}

bool Power_Control_Check_Battery_Limit() {
  // load power configuration from EEPROM
  Power_Control_Load_Configuration();

  // check battery voltage
  bool checkPassed = true;
  if((Power_Control_Get_Battery_Voltage() <= BATTERY_VOLTAGE_LIMIT) && powerConfig.bits.lowPowerModeEnabled) {
    // activate low power mode
    powerConfig.bits.lowPowerModeActive = 1;
    checkPassed = false;
  } else {
    // deactivate low power mode
    powerConfig.bits.lowPowerModeActive = 0;
    checkPassed = true;
  }

  // save power configuration to EEPROM
  Power_Control_Save_Configuration();
  return(checkPassed);
}

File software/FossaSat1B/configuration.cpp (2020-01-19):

#include "configuration.h"

// flag to signal interrupts enabled/disabled
volatile bool interruptsEnabled = true;

// flag to signal data was received from ISR
volatile bool dataReceived = false;

// current modem configuration
uint8_t currentModem;

// current spreading factor mode
uint8_t spreadingFactorMode;

// timestamps
uint32_t lastHeartbeat = 0;

// INA226 instance
INA226 ina;

// RadioLib instances
SX1268 radio = new Module(RADIO_NSS, RADIO_DIO1, RADIO_NRST, RADIO_BUSY);
MorseClient morse(&radio);

// transmission password
const char* password = "password";

// encryption key
const uint8_t encryptionKey[] = {0x01, 0x02, 0x03, 0x04, 0x05, 0x06, 0x07, 0x08,
                                 0x09, 0x0a, 0x0b, 0x0c, 0x0d, 0x0e, 0x0f, 0x00};

void Configuration_Setup_Pins() {
  // set up digital pins
  pinMode(DIGITAL_OUT_MOSFET_1, OUTPUT);
  pinMode(DIGITAL_OUT_MOSFET_2, OUTPUT);
  pinMode(DIGITAL_OUT_WATCHDOG_HEARTBEAT, OUTPUT);
  pinMode(DIGITAL_OUT_MPPT_PIN, OUTPUT);

  // set up analog pins
  pinMode(ANALOG_IN_SOLAR_A_VOLTAGE_PIN, INPUT);
  pinMode(ANALOG_IN_SOLAR_B_VOLTAGE_PIN, INPUT);
  pinMode(ANALOG_IN_SOLAR_C_VOLTAGE_PIN, INPUT);
  pinMode(ANALOG_IN_RANDOM_SEED, INPUT);

  // bring deployment MOSFETs low
  digitalWrite(DIGITAL_OUT_MOSFET_1, LOW);
  digitalWrite(DIGITAL_OUT_MOSFET_2, LOW);

  // provide seed for encrpytion PRNG
  randomSeed(analogRead(ANALOG_IN_RANDOM_SEED));
}

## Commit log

2019-12-16 Imported code from FOSSASAT-1
    [configuration.h]
2019-12-16 Fixed non-deafult parameters
    [configuration.h]
2020-01-09 Updated to RadioLib 3.0.0
    [configuration.h]
2020-01-17 Added CW-synced FS-1B version
    [configuration.h]
2020-01-17 Added output power test
2020-01-18 Added deployment debug
    [configuration.h]
2020-01-18 Set default values for debug macros
    [configuration.h]
2020-01-18 Fixed incorrect function names
    [FossaSat1B.ino]
2020-01-18 Simplified INA226 I2C transaction (FOSSASAT-1/#3)
2020-01-18 Updated CW beep limit
    [configuration.h]
2020-01-18 Added missing battery check
    [FossaSat1B.ino]
2020-01-18 Added sleep length overhead compensation
    [configuration.h]
2020-01-18 documented most of the configuration.h
    [configuration.h]
2020-01-19 Adjusted doygen comments formatting
    [configuration.h]
2020-01-19 finished documenting and added tests
    [configuration.h]
2020-01-19 spelling mistakes
    [configuration.h]
2020-01-19 documented the communications header.
    [configuration.h]
2020-01-19 documented the power control header and added tests
2020-01-19 added explanation to power control charge function
2020-01-20 Added missing macro definition
    [configuration.h]
2020-01-20 cppcheck fixed, all green now
    [FossaSat1B.ino]
2020-01-20 Removed all dynamic allocations
    [configuration.h]
2020-01-20 docker update: * dockerfile updated to be able to compile arduino stuff * travis update * gitignore will ignore now binary from arduino
2020-01-21 Decresed buffer size
    [configuration.h]
2020-01-21 Added EEPROM definitions for rx lengths
    [configuration.h]
2020-01-21 Added option to use static only memory management
    [configuration.h]
2020-01-21 Increased FSK rx bandwidth
    [configuration.h]
2020-01-22 Uploaded Gerbers and PCB Files
    [Gerber_BoardOutline.GKO, Gerber_BottomLayer.GBL, Gerber_BottomPasteMaskLayer.GBP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]
2020-01-22 Added Schematics
2020-01-22 switch travis to use docker
2020-01-23 Lowered morse speed to 20 wpm
    [configuration.h]
2020-01-23 Changed morse voltage from number to code
2020-01-23 Added misisng constants
    [configuration.h]
2020-01-23 Added function to check low power battery limit
2020-01-23 Added voltage limit todo
    [configuration.h]
2020-01-23 Added voltage checing during transmissions
2020-01-23 Added new counters to EEPROM map
    [configuration.h]
2020-01-23 Implemented frame counters
2020-01-23 Added frame counters to RESP_LAST_PACKET_INFO
2020-01-23 Removed resolved todo
    [configuration.h]
2020-01-23 Adjusted size of static arrays
    [configuration.h]
2020-01-23 Changed packet info frame building
2020-01-23 Added demo ground station sketch
2020-01-23 Extended EEPROM map for stats logging
    [configuration.h]
2020-01-23 Added check to not send LoRa system info in low power mode
2020-01-23 Removed unused constants
    [configuration.h]
2020-01-24 Added ground station packet counters readout
2020-01-24 Changed stats sizes in EEPROM
    [configuration.h]
2020-01-24 Fixed incorrect callsing EEPROM address range
    [configuration.h]
2020-01-25 Resolved todos
    [configuration.h]
2020-01-25 Removed stale todo
    [configuration.h]
2020-01-25 Set receive intervals to half in low power mode
2020-01-25 Added missing transmission control checks to CW beacon
    [FossaSat1B.ino]
2020-01-25 Added missing macro parenthesis
    [configuration.h]
2020-01-25 Fixed debug output format
    [FossaSat1B.ino]
2020-01-25 Changed data ordering in system info frame
2020-01-25 Updated order of system information in ground station demo
2020-01-27 Set default OCP to 140 mA
    [configuration.h]
2020-01-27 Added return value to battery check function
2020-01-27 Added check for battery level during solar cell recording
2020-01-29 Set required RadioLib version to 3.2.1 (PA fixes)
    [FossaSat1B.ino]
2020-01-29 Fixed private/public frame check
2020-01-29 Added TCXO voltage configuration
2020-02-01 Added todo
    [configuration.h]
2020-02-06 Added EEPROM wipe sketch
    [configuration.h]
2020-03-23 Set initial LFSR value to 0x1FF for SX127x compatibility
    [configuration.h]
2020-04-14 Fixed outdated NC macro name
    [configuration.h]
2020-05-07 Removed some debug output to fit into memory with debug enabled
    [configuration.h]
2020-05-14 Set static only build option
    [configuration.h]
2020-05-17 Fixed typo in function name
    [FossaSat1B.ino, power_control.cpp]
2020-05-17 Set watchdog reset sleep length to 4x 8-sec cycles
    [configuration.h]
2020-05-17 Disabled morse preamble
    [configuration.h]
2020-05-17 Set Morse beacon to transmit only every 2nd loop
    [configuration.h]
2020-05-18 Removed EEPROM_WIPE macro
    [configuration.h]
2020-05-18 Fixed uptime calculation for Morse beacon
    [FossaSat1B.ino]
2020-05-18 Removed static only macro
    [configuration.h]
2020-05-18 Updated EEPROM map in wipe sketch
    [configuration.h]
2020-05-21 Removed outdate comment
    [configuration.h]
2020-05-21 Set response delay to 500 ms
    [configuration.h]
2020-05-21 Set FSK carrier frequency tot 436.8 MHz
    [configuration.h]
2020-05-22 Added automated deployment after elapsed time
    [configuration.h]
2020-05-22 Added option to skip battery management on watchdog update
    [pin_interface.cpp, power_control.cpp]
2020-05-24 Set deployment sleep length to 30 minutes
    [configuration.h]
2020-05-26 Added automated system info wipe during integration reset
    [configuration.h]
2020-05-28 Added variable CW beep interval based on battery voltage
2020-05-29 Fixed battery voltage beep interval check
    [FossaSat1B.ino]
2020-06-15 switch to PIO
    [configuration.h]
2020-06-17 move tests which are not automaticaly check into seperat folder
    [configuration.h]
2020-06-25 moved src folder back
    [configuration.h]
2020-07-06 Removed redundant DIO2 RF switch call (enabled by default in RadioLib)
2020-07-06 Added missing LoRa preamble length parameter
    [configuration.h]
2020-07-06 Updated ground station demo for RadioLib 4.0.0
    [configuration.h]
2020-07-06 changed filenames to prevent conflicts
    [main.cpp]
2020-07-08 convert to pio
    [configuration.h]
2020-07-09 esp32 version for GroundStation
    [configuration.h]
2020-07-10 added interval checking when power modes change
2020-07-10 Revert "esp32 version for GroundStation"
    This reverts commit de2f2662a52c3b48253d05a45085bdae54cb16cd.
    [configuration.h]
2020-07-11 print timestamp infront of every line to get timing
2020-07-28 Fixed voltage unit
2020-07-28 Fixed delay length between CW beeps
    [FossaSat1B.ino]
